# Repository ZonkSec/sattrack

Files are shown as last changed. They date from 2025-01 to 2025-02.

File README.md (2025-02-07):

# SatTrack
DIY Satellite Tracker for Ham Radio
* For [Arrow II Sat Antenna](https://www.arrowantennas.com/arrowii/146-437.html)
* improved 3D printed parts | [original design by jbyrns](https://www.thingiverse.com/thing:4664558)
* Nema 17 Motors
* on-board tracking software and battery
  * doubles as a counter weight; fewer wires to get tangled 
  * rasperby pi zero
  * custom pcb for:
    * A4988 Stepper Drivers
    * Power regulation
    * Buzzer output
    * Easy connectivity for switches and connections
  * full featured web interface
  * satellite definitions compatible with opengd77
 
 ## Repo Structure
 The repo is broken into several categories:
 * [3d models](3d%20models) - this contains all the 3d parts, as well as hardware needed
 * [app](app) - this contains the python application
 * [hardware](hardware) - this contains the custom pcb

Each category contains it's own readme.md with more details.

 ## Images
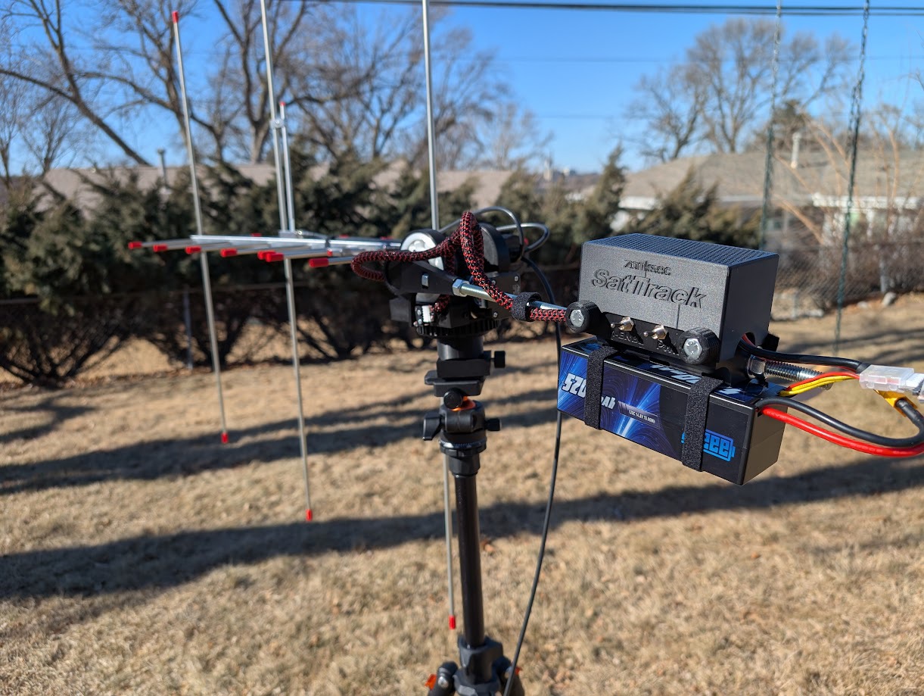
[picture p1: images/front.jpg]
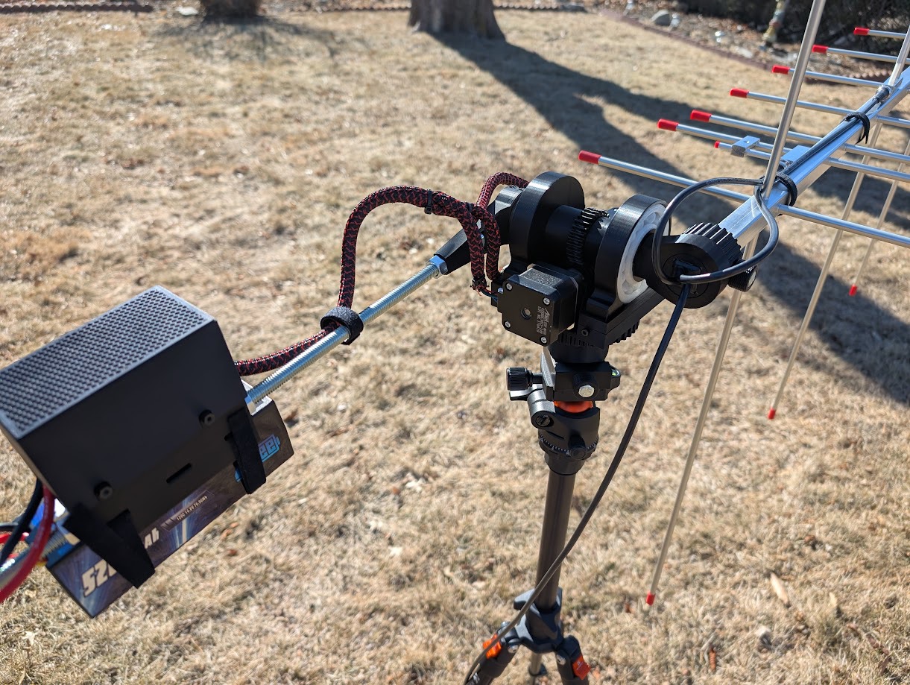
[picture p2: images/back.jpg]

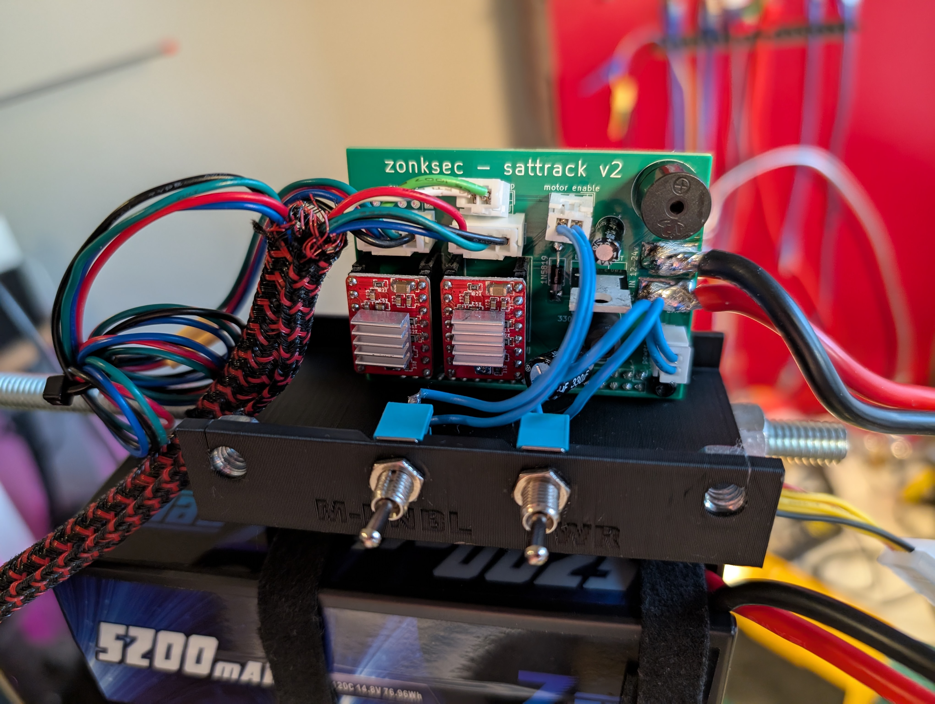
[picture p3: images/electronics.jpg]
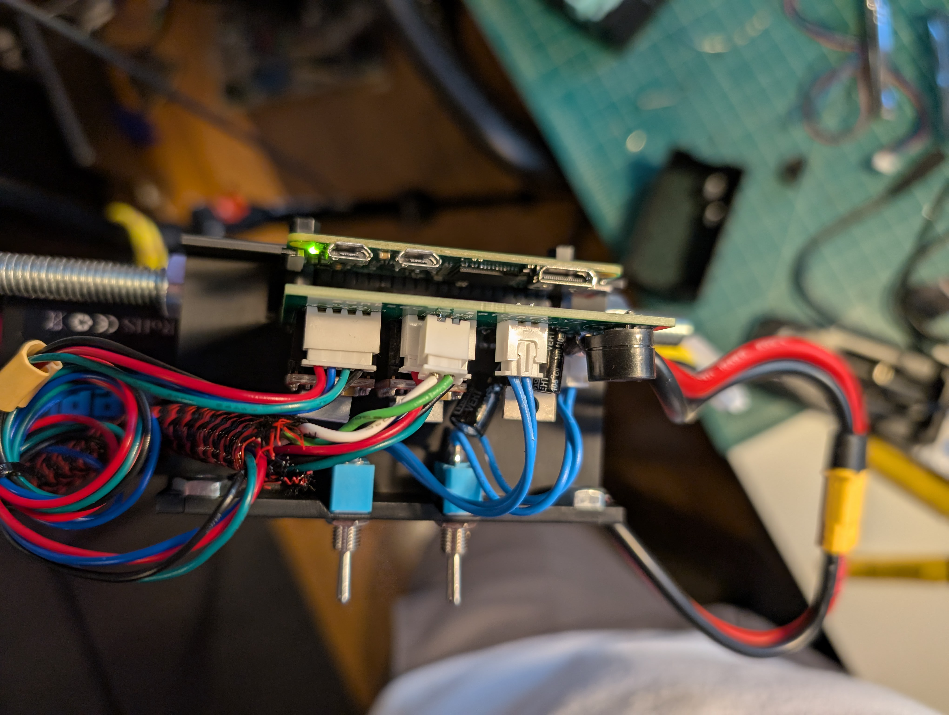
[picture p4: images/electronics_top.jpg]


<div align="center">
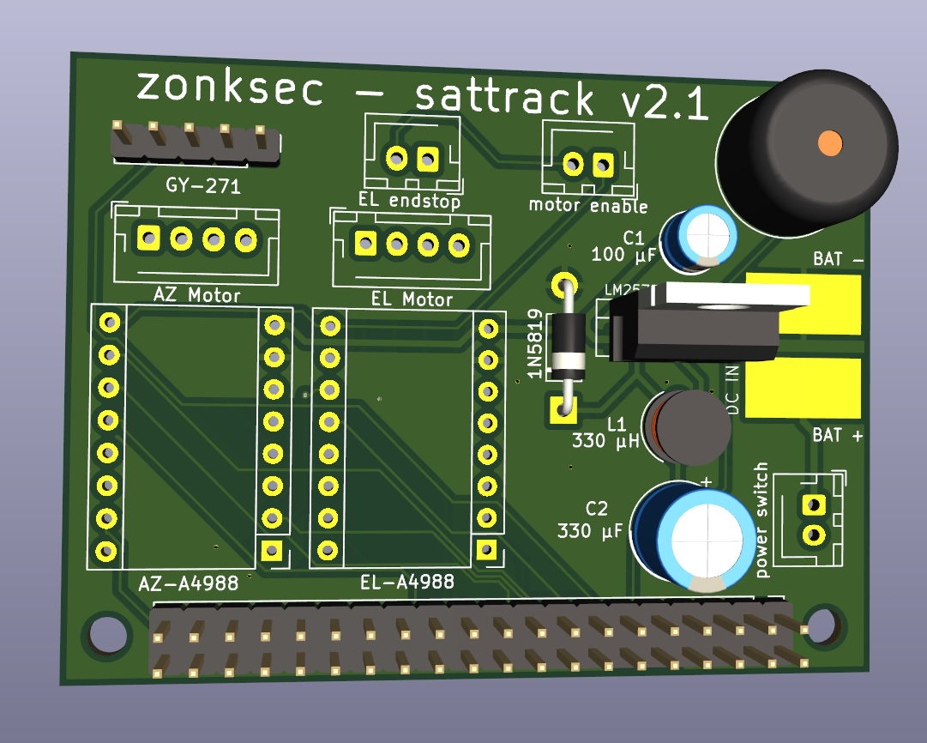
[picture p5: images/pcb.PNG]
 
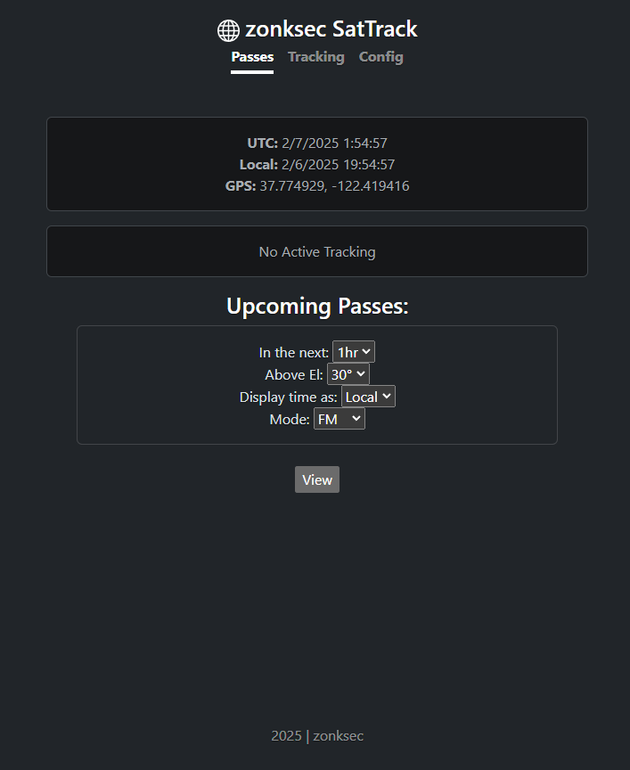
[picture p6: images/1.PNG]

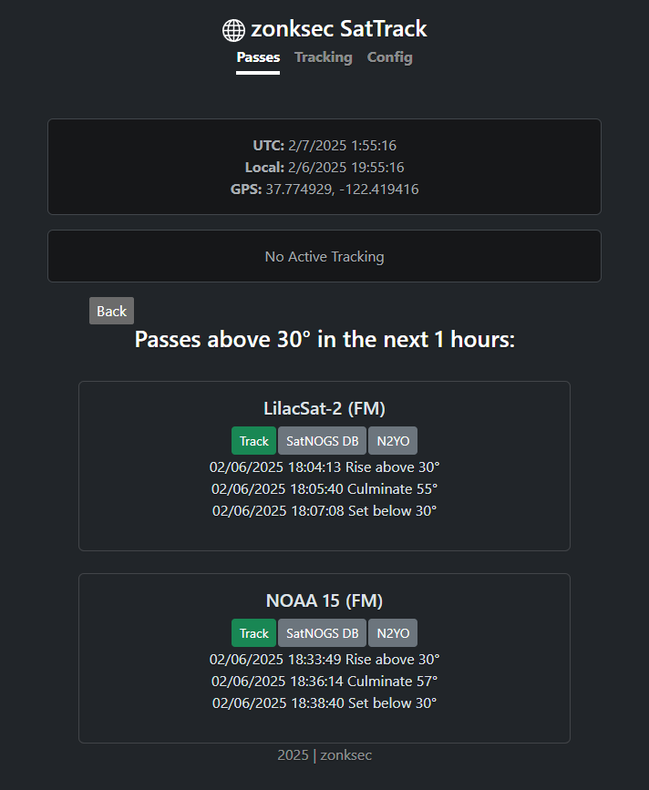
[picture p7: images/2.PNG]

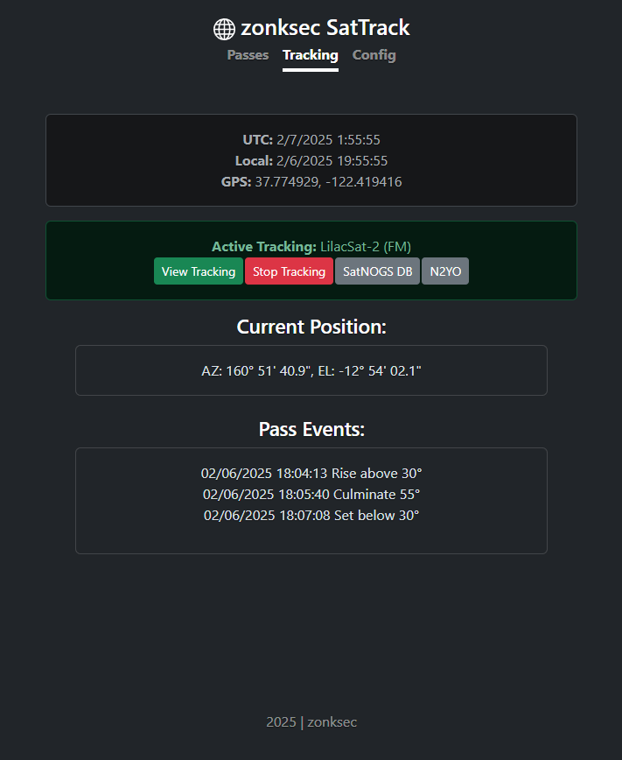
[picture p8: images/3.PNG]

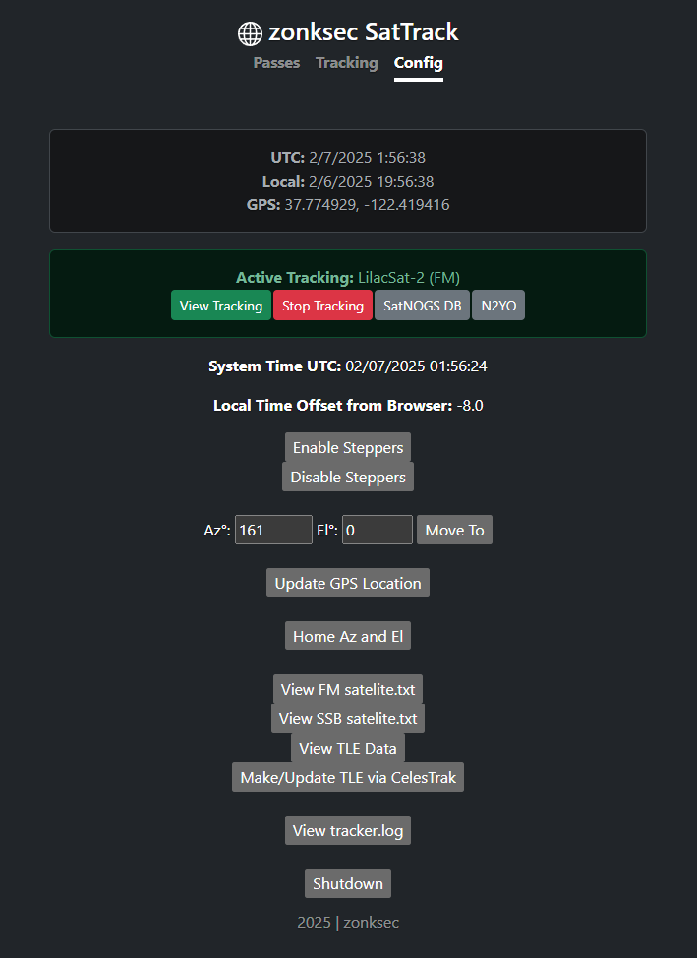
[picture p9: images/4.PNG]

</div>

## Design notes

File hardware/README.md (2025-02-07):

# Hardware

## Parts Needed:
* 1x Custom PCB
* 1x Raspberry Pi Zero W 1 or 2 (other RPis may work, but these are the only I've tested)
* 2x A4988 Stepper Drivers
* 2x "3d pritner" motor wires (depends on your motor, but mine was the standard 4pin XH 2.54 <-> 6pin PH 2.0)
* 2x Nema 17 Stepper Motors
* 1x 100 µF capacitor (C1)
* 1x 330 µF capacitor (C2)
* 1x 1N5819 Diode (D1)
* 1x 330 µH inductor (L1)
* 1x LM2575 5v switching reg (U1)
* 1x Passive Buzzer (BZ1)
* 2x Mini Toggle Switches ([Link](https://www.amazon.com/dp/B0799LBFNY?))
* 3x JST-XH 2.5pitch 2pin parts for motor enable switch, on/off switch, EL endspot microswitch
* 2x JST-XH 2.5pitch 4pin parts for motor connectors
* 1x Micro Limit Switch KW12-3 for EL limit switch
* 1x Battery connector and wires (I used XT60)
* 1x LiPo Battery ([Link to what I use](https://www.amazon.com/gp/product/B0D59XCQ3Z))
* 1x Roll of 1/2in Hook & Loop Straps to strap battery on
* 1x RC Battery Alarm to monitor voltage

<div align="center">

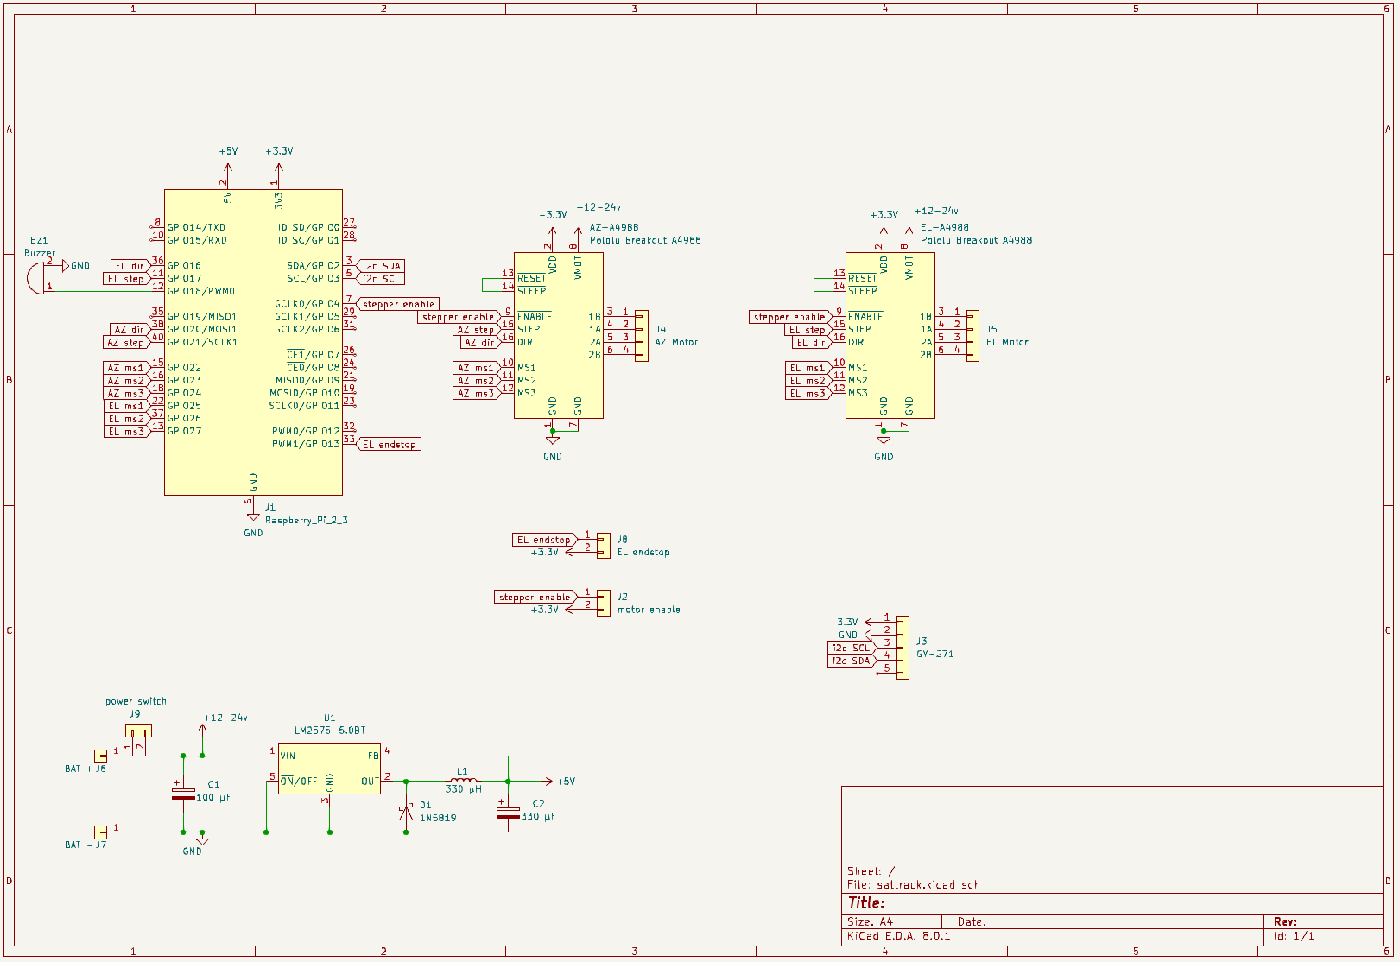
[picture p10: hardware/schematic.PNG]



</div>

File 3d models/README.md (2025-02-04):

# 3D Models
Original credit goes to jbyrns - https://www.thingiverse.com/thing:4664558

## Revised
* revised_Base.stl - made main bolt have a hex top, so can be tighted from below after assembly and wont spit
* revised_Counter.stl - changed this counter weight arm to have neccessary spacing to make room for microswitch EL endstop
* revised_GearSmall.stl - changed this gear to fit standard m3 nut snuggly 
* revised_Thrust.stl - made room so this part can accomadate the bolt and nut, while still fitting in tripod
* revised_WormConnector.stl - changed this gear to fit standard m3 nut snuggly 
  
## New
* new_EBbox_base.stl - electronic battery box bottom. this serves as the counter weight 
* new_EBbox_top.stl - electronic battery box top. this serves as the counter weight 
* new_endstop_arm.stl - this arm is engaged with main shaft (TrackArm) and can be used to home/zero the EL axis using a microswitch
* new_endstop_switch_bracket.stl - this bracket holds the microswitch for EL homing. bolts onto Base.stl
* new_quaterinch_knob.stl - knob for 1/4 bolt. used in adapter plate, trackarmknob, and EBbox
* new_universal_adapter_plate.stl - adapter plate for tripods whose quick release doesnt fit Thrust.stl. can attach to any 1/4 threaded plate
* new_wrench.stl - wrench to tighten parts on the 3/8th threaded rod.
  
## Original
* original_BearingHousing.STL
* original_Clip.STL
* original_Gear.STL
* original_TrackArm.STL
* original_TrackArmKnob.STL
* original_Worm.STL
* original_WormBase.STL
* original_bearing_all_fixed.stl
* original_collar.STL

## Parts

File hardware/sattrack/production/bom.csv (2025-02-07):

Designator | Footprint | Quantity | Value | LCSC Part #
AZ-A4988, EL-A4988 | Pololu_Breakout-16_15.2x20.3mm | 2 | Pololu_Breakout_A4988
BZ1 | Buzzer_12x9.5RM7.6 | 1 | Buzzer
C1 | CP_Radial_D5.0mm_P2.50mm | 1 | 100 µF
C2 | CP_Radial_D8.0mm_P3.80mm | 1 | 330 µF
D1 | D_DO-41_SOD81_P10.16mm_Horizontal | 1 | 1N5819
J1 | PinHeader_2x20_P2.54mm_Vertical | 1 | Raspberry_Pi_2_3
J2 | JST_XH_B2B-XH-AM_1x02_P2.50mm_Vertical | 1 | motor enable
J3 | PinHeader_1x05_P2.54mm_Vertical | 1 | GY-271
J4 | JST_XH_B4B-XH-AM_1x04_P2.50mm_Vertical | 1 | AZ Motor
J5 | JST_XH_B4B-XH-AM_1x04_P2.50mm_Vertical | 1 | EL Motor
J6 | SolderWirePad_1x01_SMD_5x10mm | 1 | BAT +
J7 | SolderWirePad_1x01_SMD_5x10mm | 1 | BAT -
J8 | JST_XH_B2B-XH-AM_1x02_P2.50mm_Vertical | 1 | EL endstop
J9 | JST_XH_B2B-XH-AM_1x02_P2.50mm_Vertical | 1 | power switch
L1 | L_Radial_D6.0mm_P4.00mm | 1 | 330 µH
U1 | TO-220-5_Vertical | 1 | LM2575-5.0BT

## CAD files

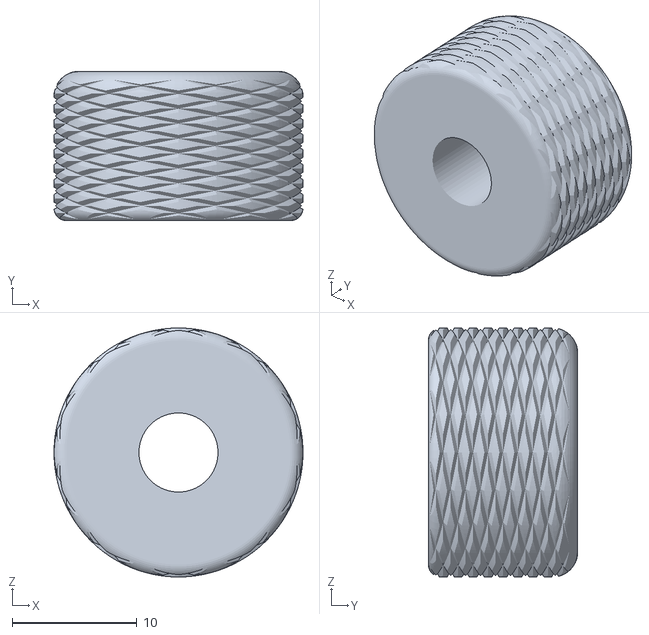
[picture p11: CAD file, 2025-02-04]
3d models/new_quaterinch_knob.stl
20.0 x 12.0 x 20.0

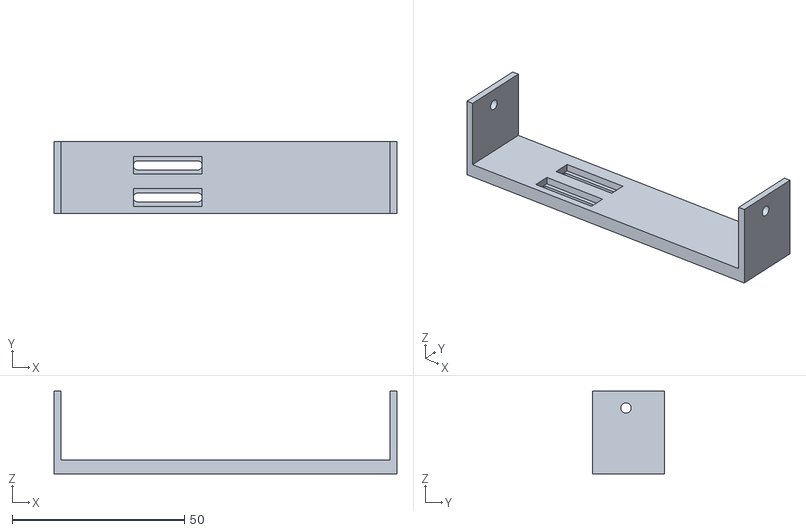
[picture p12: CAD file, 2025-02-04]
3d models/new_endstop_switch_bracket.stl
99.5 x 21.0 x 24.0

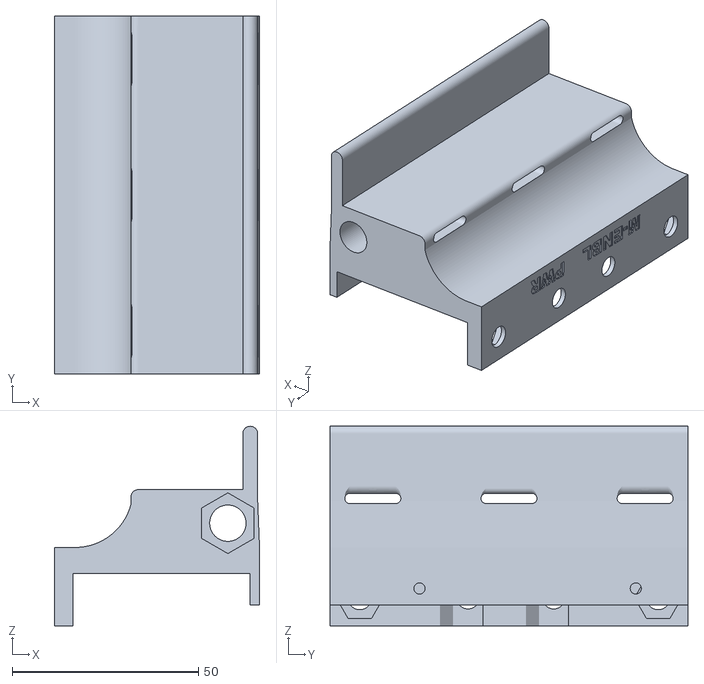
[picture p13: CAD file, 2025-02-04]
3d models/new_EBbox_base.stl
55.0 x 96.0 x 53.5

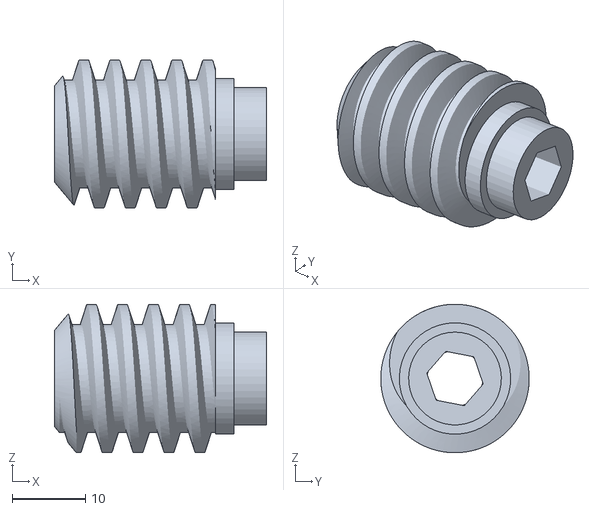
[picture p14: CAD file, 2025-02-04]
3d models/original_Worm.STL
29.0 x 20.3 x 20.3

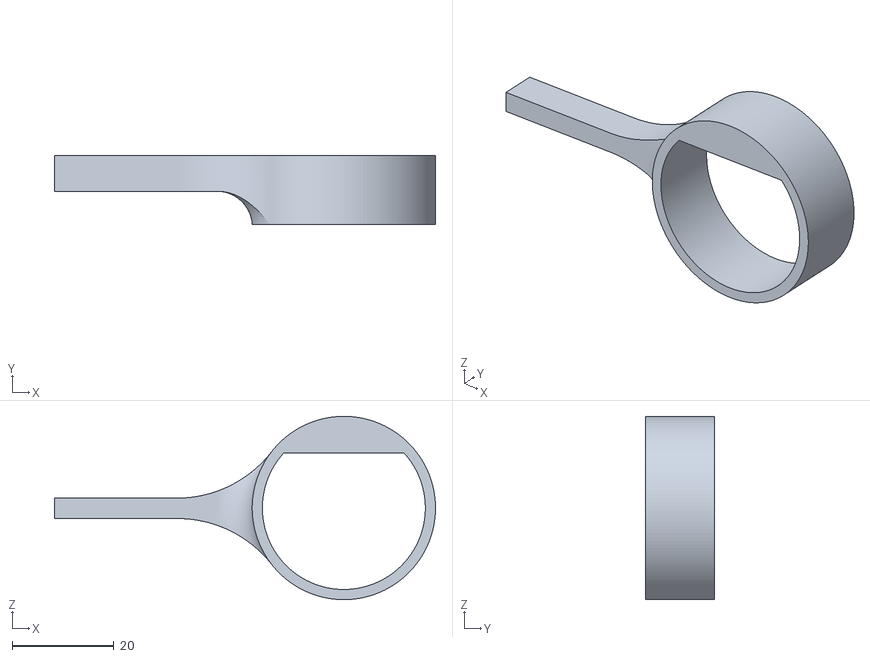
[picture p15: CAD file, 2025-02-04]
3d models/new_endstop_arm.stl
74.8 x 13.5 x 36.0

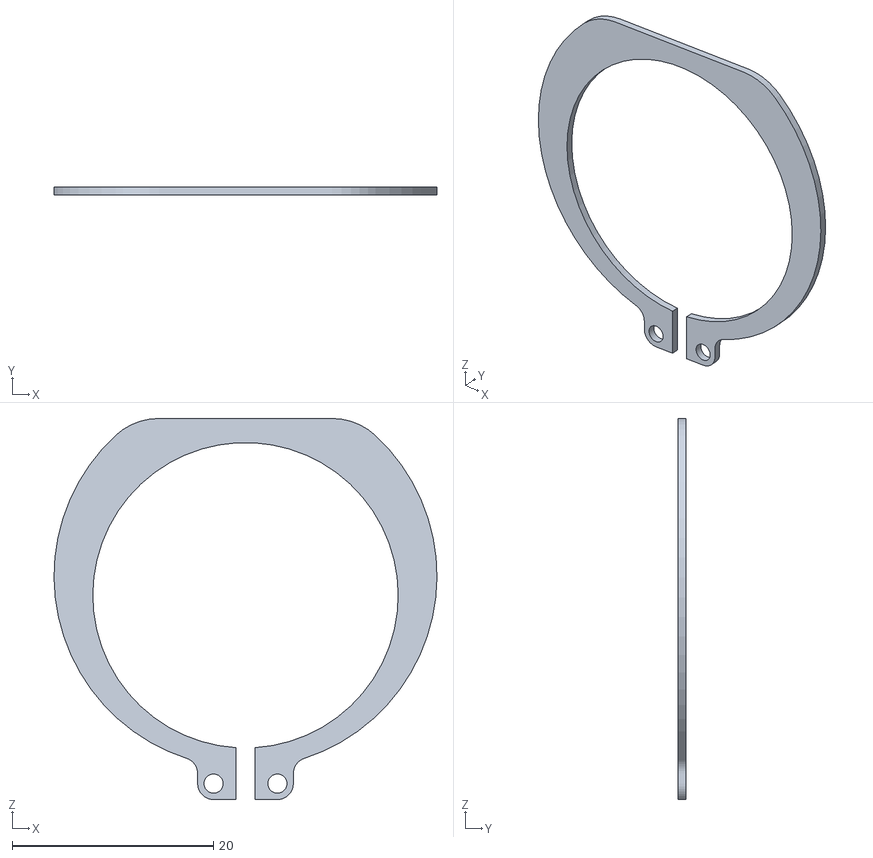
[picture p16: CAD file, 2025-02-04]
3d models/original_Clip.STL
38.1 x 0.826 x 37.9

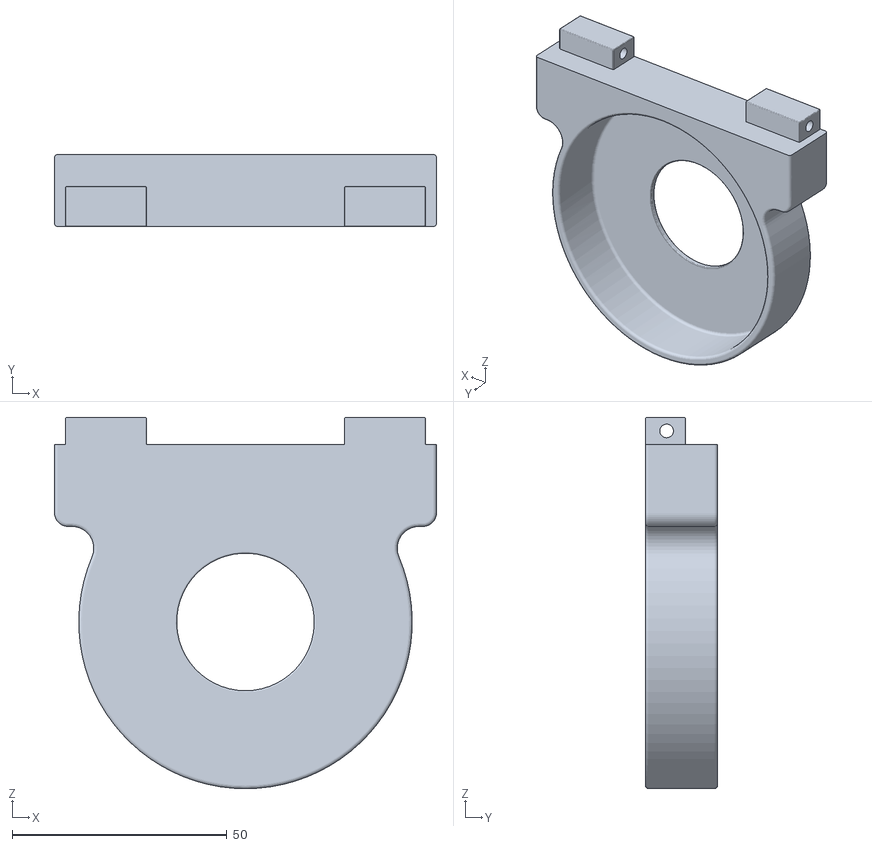
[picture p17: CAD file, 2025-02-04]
3d models/original_BearingHousing.STL
88.9 x 16.8 x 86.4

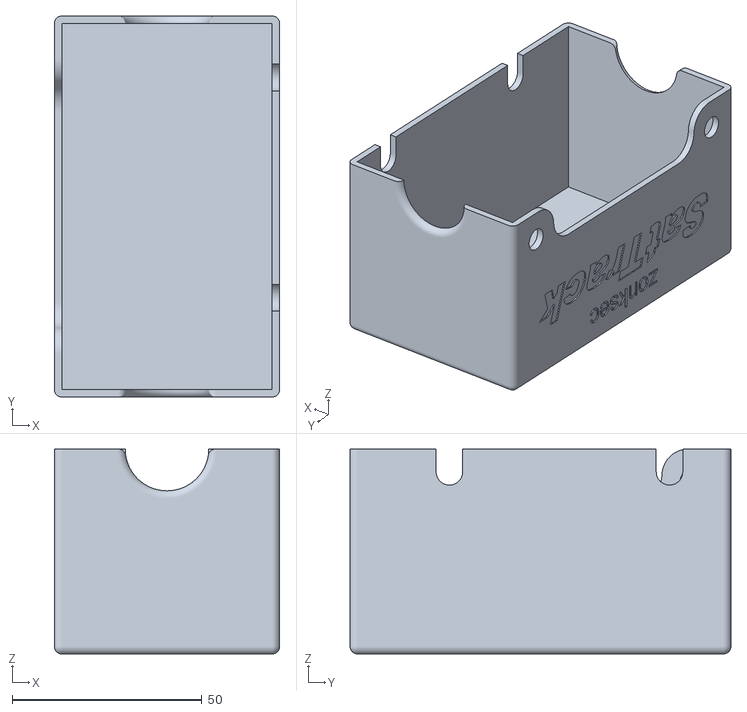
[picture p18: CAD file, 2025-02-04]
3d models/new_EBbox_top.stl
59.4 x 100.4 x 54.0

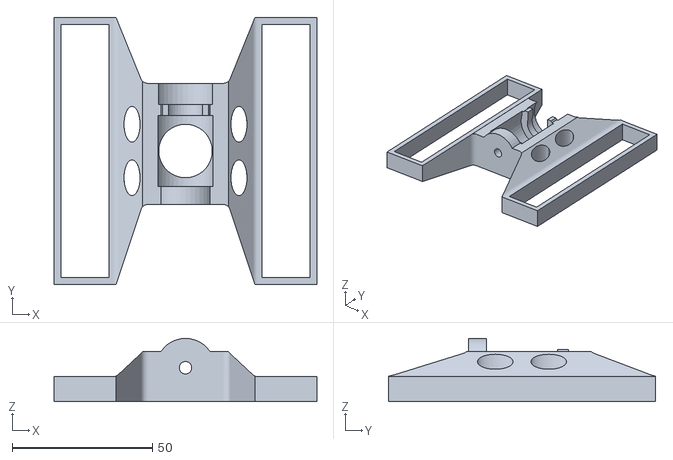
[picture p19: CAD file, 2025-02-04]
3d models/original_WormBase.STL
93.7 x 95.3 x 22.5

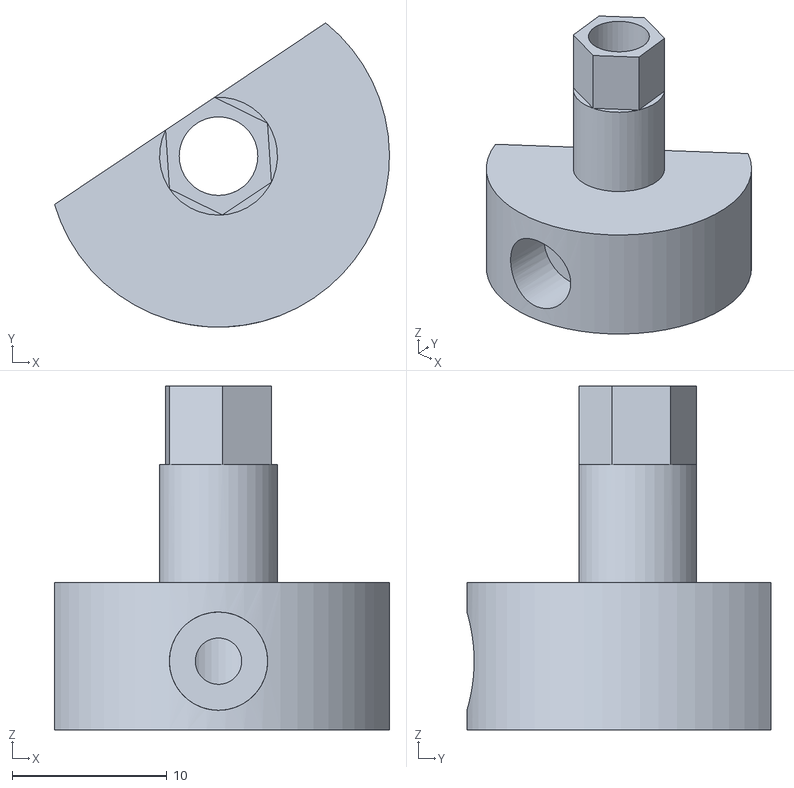
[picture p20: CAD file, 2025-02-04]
3d models/revised_WormConnector.stl
21.6 x 19.7 x 22.2

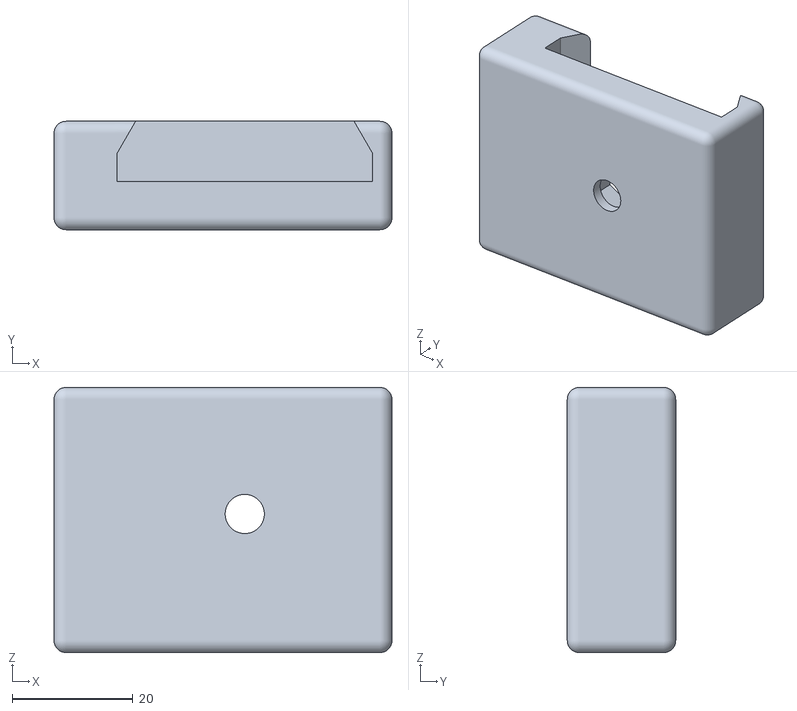
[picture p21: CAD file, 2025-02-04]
3d models/new_universal_adapter_plate.stl
56.1 x 18.0 x 44.0

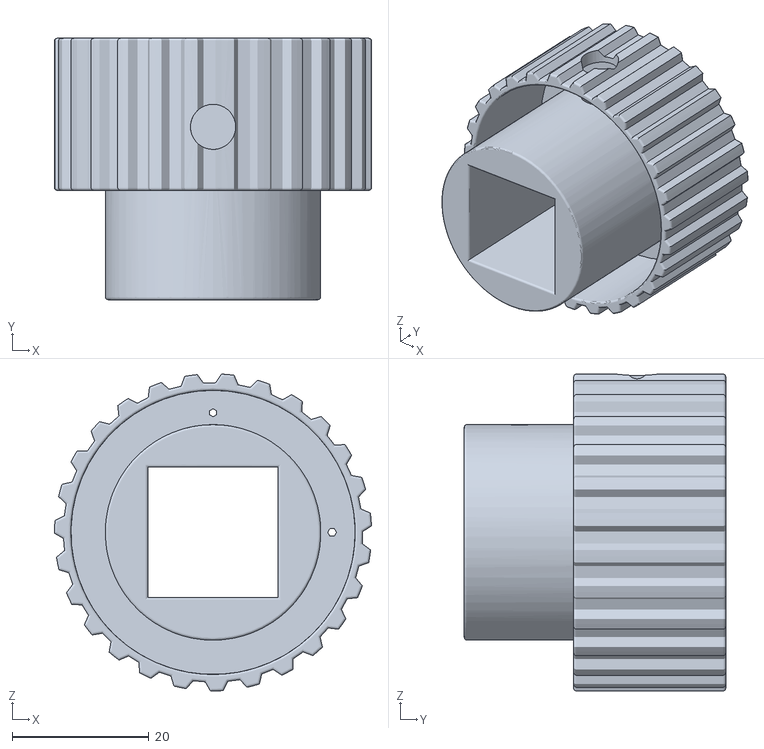
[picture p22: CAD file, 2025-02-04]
3d models/original_TrackArmKnob.STL
46.3 x 38.2 x 46.3

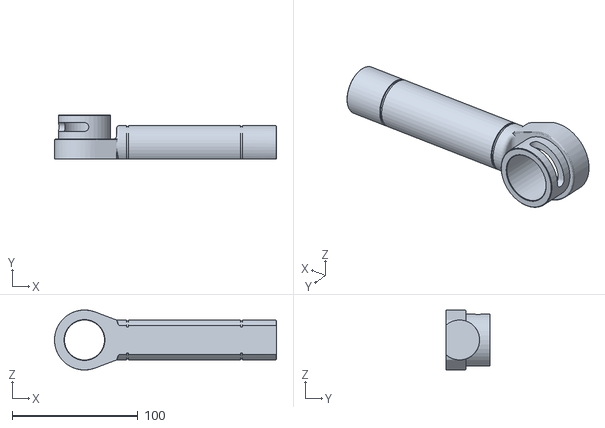
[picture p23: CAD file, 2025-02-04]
3d models/original_TrackArm.STL
176.2 x 34.9 x 47.6

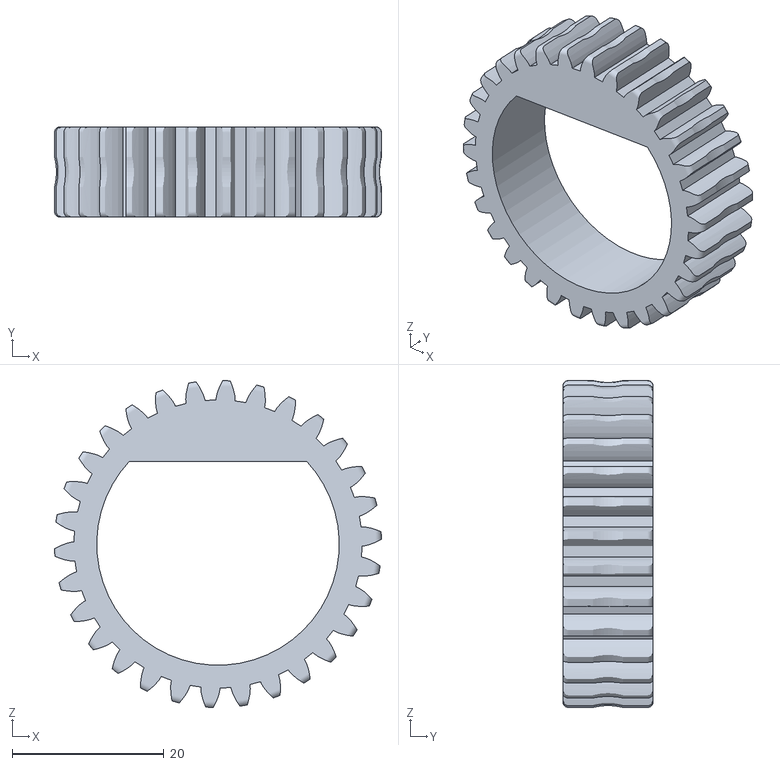
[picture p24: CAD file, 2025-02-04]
3d models/original_Gear.STL
43.2 x 11.9 x 43.2

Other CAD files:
3d models/new_wrench.stl
3d models/revised_Base.stl
3d models/revised_Thrust.stl
3d models/revised_GearSmall.stl
3d models/original_bearing_all_fixed.stl
3d models/original_collar.STL
3d models/revised_Counter.stl

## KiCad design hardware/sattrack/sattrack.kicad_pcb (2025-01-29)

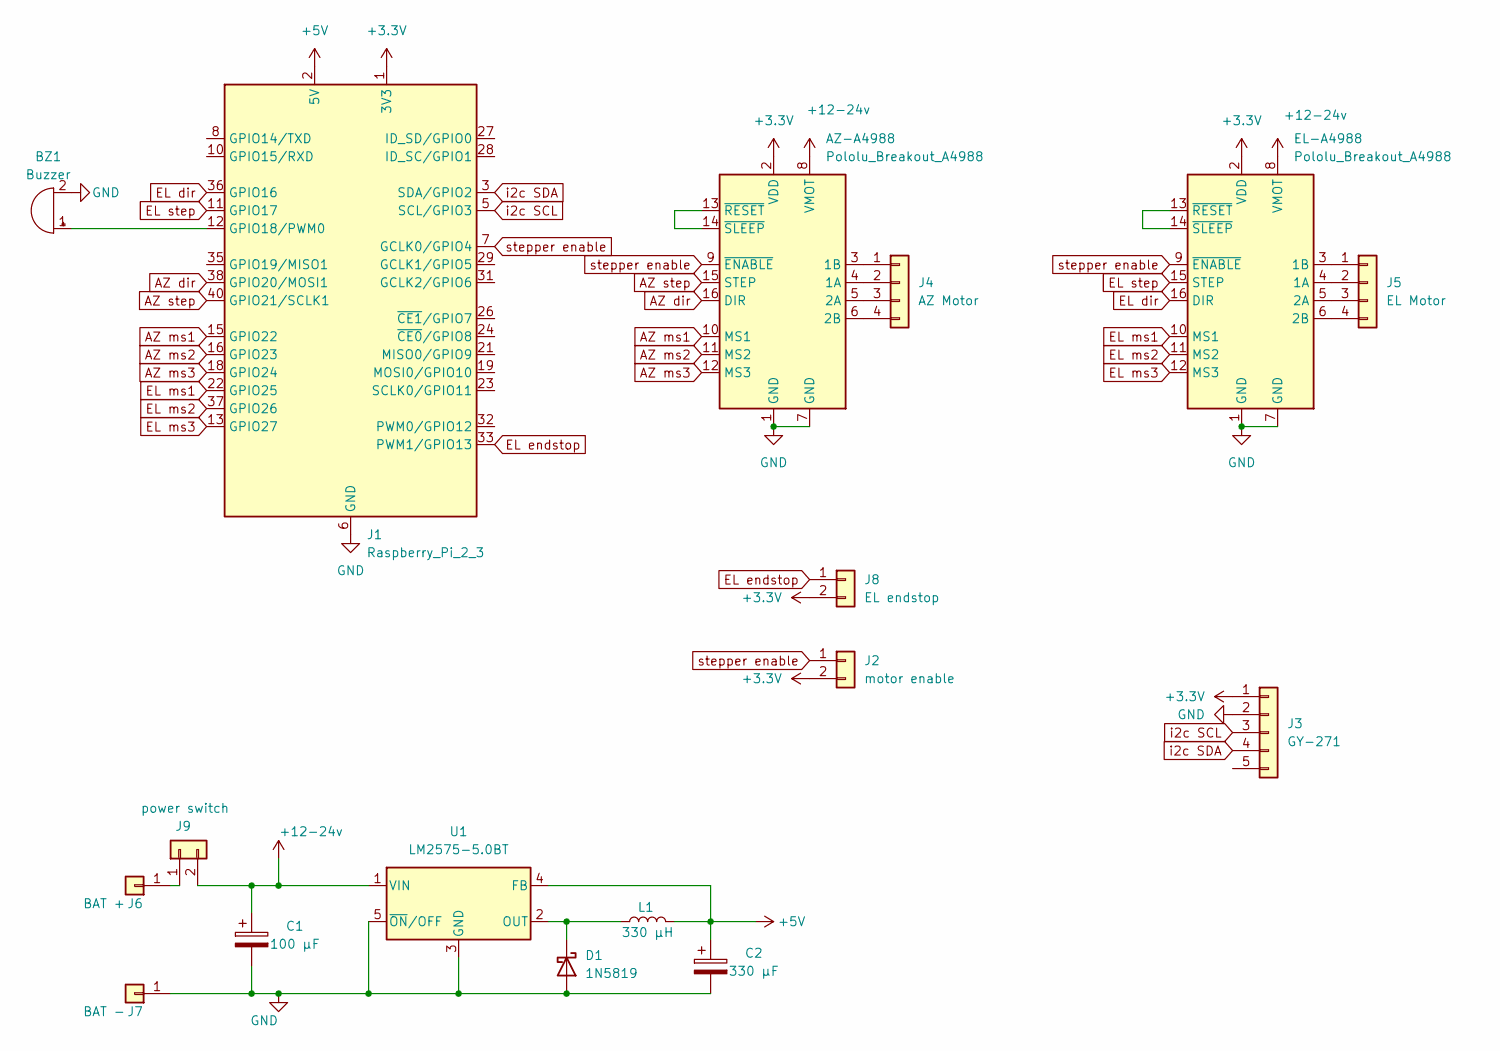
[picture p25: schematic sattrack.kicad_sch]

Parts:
AZ-A4988: Pololu_Breakout_A4988; Pololu_Breakout-16_15.2x20.3mm
BZ1: Buzzer; Buzzer_12x9.5RM7.6
C1: 100 µF; CP_Radial_D5.0mm_P2.50mm
C2: 330 µF; CP_Radial_D8.0mm_P3.80mm
D1: 1N5819; D_DO-41_SOD81_P10.16mm_Horizontal
EL-A4988: Pololu_Breakout_A4988; Pololu_Breakout-16_15.2x20.3mm
J1: Raspberry_Pi_2_3; PinHeader_2x20_P2.54mm_Vertical
J2: motor enable; JST_XH_B2B-XH-AM_1x02_P2.50mm_Vertical
J3: GY-271; PinHeader_1x05_P2.54mm_Vertical
J4: AZ Motor; JST_XH_B4B-XH-AM_1x04_P2.50mm_Vertical
J5: EL Motor; JST_XH_B4B-XH-AM_1x04_P2.50mm_Vertical
J6: BAT +; SolderWirePad_1x01_SMD_5x10mm
J7: BAT -; SolderWirePad_1x01_SMD_5x10mm
J8: EL endstop; JST_XH_B2B-XH-AM_1x02_P2.50mm_Vertical
J9: power switch; JST_XH_B2B-XH-AM_1x02_P2.50mm_Vertical
L1: 330 µH; L_Radial_D6.0mm_P4.00mm
U1: LM2575-5.0BT; TO-220-5_Vertical

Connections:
+3.3V: AZ-A4988.2 (VDD), EL-A4988.2 (VDD), J1.1 (3V3), J1.17 (3V3), J2.2, J3.1, J8.2
+5V: C2.1, J1.2 (5V), J1.4 (5V), L1.2, U1.4 (FB)
+12-24v: AZ-A4988.8 (VMOT), C1.1, EL-A4988.8 (VMOT), J9.2, U1.1 (VIN)
AZ dir: AZ-A4988.16 (DIR), J1.38 (GPIO20/MOSI1)
AZ ms1: AZ-A4988.10 (MS1), J1.15 (GPIO22)
AZ ms2: AZ-A4988.11 (MS2), J1.16 (GPIO23)
AZ ms3: AZ-A4988.12 (MS3), J1.18 (GPIO24)
AZ step: AZ-A4988.15 (STEP), J1.40 (GPIO21/SCLK1)
EL dir: EL-A4988.16 (DIR), J1.36 (GPIO16)
EL endstop: J1.33 (PWM1/GPIO13), J8.1
EL ms1: EL-A4988.10 (MS1), J1.22 (GPIO25)
EL ms2: EL-A4988.11 (MS2), J1.37 (GPIO26)
EL ms3: EL-A4988.12 (MS3), J1.13 (GPIO27)
EL step: EL-A4988.15 (STEP), J1.11 (GPIO17)
GND: AZ-A4988.1 (GND), AZ-A4988.7 (GND), BZ1.2 (-), C1.2, C2.2, D1.2 (A), EL-A4988.1 (GND), EL-A4988.7 (GND), J1.6 (GND), J1.9 (GND), J1.14 (GND), J1.20 (GND), J1.25 (GND), J1.30 (GND), J1.34 (GND), J1.39 (GND), J3.2, J7.1, U1.3 (GND), U1.5 (~ON/OFF)
unnamed: AZ-A4988.4 (1A), J4.2
unnamed: AZ-A4988.3 (1B), J4.1
unnamed: AZ-A4988.5 (2A), J4.3
unnamed: AZ-A4988.6 (2B), J4.4
unnamed: AZ-A4988.13 (~RESET), AZ-A4988.14 (~SLEEP)
unnamed: BZ1.1 (+), J1.12 (GPIO18/PWM0)
unnamed: D1.1 (K), L1.1, U1.2 (OUT)
unnamed: EL-A4988.4 (1A), J5.2
unnamed: EL-A4988.3 (1B), J5.1
unnamed: EL-A4988.5 (2A), J5.3
unnamed: EL-A4988.6 (2B), J5.4
unnamed: EL-A4988.13 (~RESET), EL-A4988.14 (~SLEEP)
unnamed: J6.1, J9.1
i2c SCL: J1.5 (SCL/GPIO3), J3.3
i2c SDA: J1.3 (SDA/GPIO2), J3.4
stepper enable: AZ-A4988.9 (~ENABLE), EL-A4988.9 (~ENABLE), J1.7 (GCLK0/GPIO4), J2.1

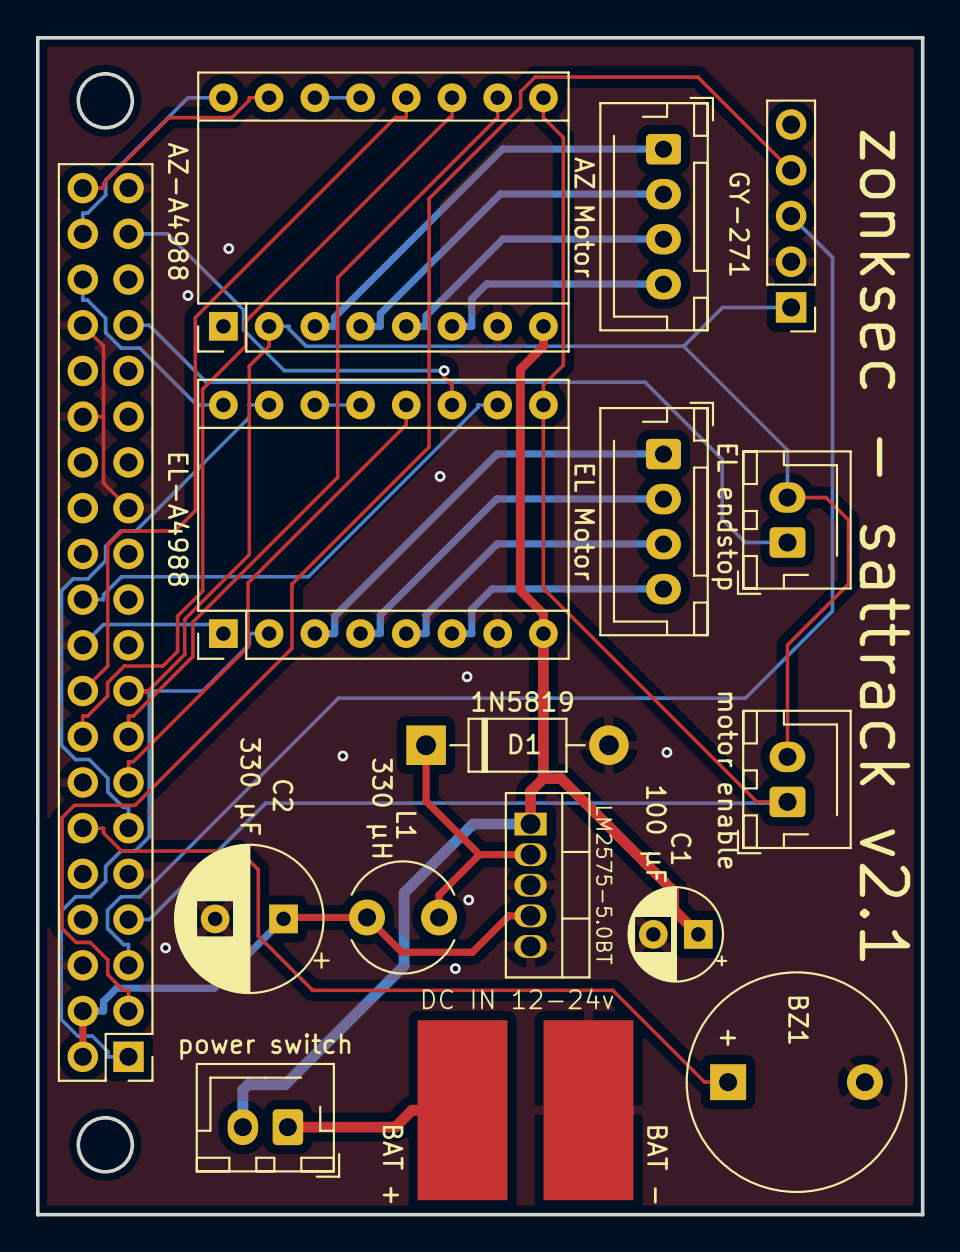
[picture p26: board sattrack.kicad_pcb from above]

Board: 2 copper layers, 49.2 x 65.4 mm, 17 parts (0 on the bottom side), 31 nets.

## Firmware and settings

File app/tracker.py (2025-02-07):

import os
import threading
from io import StringIO,BytesIO
from RpiMotorLib import RpiMotorLib
from flask import Flask,request, render_template, redirect,Response
import concurrent.futures
import signal
import RPi.GPIO as GPIO
import sys
from skyfield.api import load,wgs84
from skyfield.iokit import parse_tle_file
from datetime import timedelta,timezone,datetime
from time import sleep
import requests
import csv

if not os.path.exists("key.pem") or not os.path.exists("cert.pem"):
   print("no certs found. make sure openssl is installed. generating...")
   os.system("openssl req -x509 -newkey rsa:2048 -nodes -out cert.pem -keyout key.pem -days 3650 -subj '/C=/ST=/L=/O=/CN='")

global lat
global long
global location_tz_offset
lat = None
long = None
location_tz_offset = 0

global tracking_thread
global stop_tracking
global tracking_sat_name
global tracking_sat_pos
global tracking_sat_events
global tracking_sat_cat
tracking_thread = None
stop_tracking = False
tracking_sat_pos = ""
tracking_sat_name = ""
tracking_sat_events = ""
tracking_sat_cat = ""

app = Flask(__name__)

@app.route("/config") 
def config(): 
  global lat
  global long
  global tracking_sat_name
  global current_az_pos
  global current_el_pos
  global location_tz_offset
  global tracking_sat_cat

  now = datetime.utcnow().strftime('%m/%d/%Y %H:%M:%S')

  if GPIO.input(4) == 1:
    steppers_disabled = True
  else:
    steppers_disabled = False
  
  if lat == None or long == None:
    gpsmissing = True
  else:
    gpsmissing = False
  return render_template("config.html",tracking_sat_cat=tracking_sat_cat,location_tz_offset=location_tz_offset,now=now,current_az_pos=current_az_pos,current_el_pos=current_el_pos,steppers_disabled=steppers_disabled,tracking_sat_name=tracking_sat_name,gpsmissing=gpsmissing,lat=lat,long=long)

@app.route("/set_tz") 
def set_tz_offset(): 
   global location_tz_offset
   location_tz_offset = int(request.args.get('offset'))
   return redirect(request.referrer)

@app.route("/view") 
def view():
  file = request.args.get('file')
  if file == "fmsattxt":
    try:
      with open('data/fm/satellites.txt', 'r') as file:
        file_content = file.read()
    except:
       file_content = "satellites.txt not found"
  elif file == "trackerlog":
     try:
        with open('tracker.log', 'r') as file:
           file_content = file.read()
     except:
        file_content = "tracker.log not found"
  elif file == "ssbsattxt":
    try:
      with open('data/ssb/satellites.txt', 'r') as file:
        file_content = file.read()
    except:
       file_content = "satellites.txt not found"
  else:
     if os.path.exists("data/ssb/filtered_TLE.txt") and os.path.exists("data/fm/filtered_TLE.txt"):
        fm_satellites = open('data/fm/filtered_TLE.txt', 'r').read()
        ssb_satellites = open('data/ssb/filtered_TLE.txt', 'r').read()
        file_content = fm_satellites + ssb_satellites
     else:
        file_content = "tle data missing"
  return Response(file_content, mimetype='text/plain')



@app.route('/motorEnable')
def enable():
   x = request.args.get('enabled')
   if x == "yes":
      GPIO.output(4, GPIO.LOW)
      return redirect(request.referrer)
   else:
      GPIO.output(4, GPIO.HIGH)
      return redirect(request.referrer)

@app.route('/shutdown')
def shutdown():
   os.system("sudo shutdown -h now")  
   return "Shutting down..."
   
@app.route('/homeAZEL')
def homeAZEL():
    if GPIO.input(4) == 1:
       return("steppers are disabled. not homing")
    if tracking_thread != None:
       return("actively tracking a sat. not homing")
    zero_EL()
    global current_az_pos
    current_az_pos = 0
    return redirect(request.referrer)

global moving 
moving = False
@app.route('/moveTo')
def moveTo():
    global current_az_pos
    global current_el_pos
    global tracking_thread
    global moving 

    if tracking_thread == None and moving == False:
      moving = True
      desired_az_pos = int(request.args.get('az',default=current_az_pos))
      desired_el_pos = int(request.args.get('el',default=current_el_pos))
      az_steps, az_direction = az_deg_to_steps_dir(desired_az_pos)
      el_steps,el_direction = el_deg_to_steps_dir(desired_el_pos)
      thread_move_steps(az_direction,az_steps,el_direction,el_steps)
      if az_steps > 0:
        current_az_pos = desired_az_pos
      if el_steps > 0:
          current_el_pos = desired_el_pos
      moving = False
      return redirect(request.referrer)
    else:
       return "cant manual move. active tracking is ongoing. or a manual move is active"

@app.route('/updateTLE')
def updateTLE():
    msg =update_sat_data()
    return msg

@app.route("/") 
@app.route('/passes',methods=['GET', 'POST'])
def listUpcomingPasses():
  global lat
  global long
  global tracking_sat_name
  global location_tz_offset
  global tracking_sat_cat

  if GPIO.input(4) == 1:
    steppers_disabled = True
  else:
     steppers_disabled = False

  if lat == None or long == None:
      gpsmissing = True
  else:
     gpsmissing = False

  if request.method == 'GET':
    return render_template("passes.html",method=request.method,tracking_sat_cat=tracking_sat_cat,steppers_disabled=steppers_disabled,tracking_sat_name=tracking_sat_name,gpsmissing=gpsmissing,lat=lat,long=long)
  if request.method == 'POST':
    if gpsmissing:
      return "lat or long not set"
  
    time = request.form.get('time')
    display_time = request.form.get('display_time')
    max_el = int(request.form.get('el',default=30))
    mode = request.form.get('mode')

    if time == None or max_el == None:
       return "pass input not set"

    ts = load.timescale()
    if mode == "fm":
      if os.path.exists("data/fm/filtered_TLE.txt"):
        satellites= load.tle_file('data/fm/filtered_TLE.txt')
      else:
        return "filtered_TLE not found. create it using 'Make/Update TLE via CelesTrak' on Config page"
    elif mode == "ssb":
      if os.path.exists("data/ssb/filtered_TLE.txt"):
        satellites= load.tle_file('data/ssb/filtered_TLE.txt')
      else:
        return "filtered_TLE not found. create it using 'Make/Update TLE via CelesTrak' on Config page"
    elif mode == "both":
       if os.path.exists("data/ssb/filtered_TLE.txt") and os.path.exists("data/fm/filtered_TLE.txt"):
        fm_satellites = open('data/fm/filtered_TLE.txt', 'r').read()
        ssb_satellites = open('data/ssb/filtered_TLE.txt', 'r').read()
        both = fm_satellites + ssb_satellites
        f = BytesIO(str.encode(both))
        satellites = list(parse_tle_file(f, ts))
       else:
        return "filtered_TLE not found. create it using 'Make/Update TLE via CelesTrak' on Config page"
    else:
      return "error on mode selection"

    location = wgs84.latlon(lat, long)
    if display_time == "local":
      location_tz = timezone(timedelta(hours=location_tz_offset))
    else:
       location_tz = timezone(timedelta(hours=0))

    t0 = ts.now()
    t1 = ts.utc(t0.utc_datetime() + timedelta(hours=int(time)))

    passes = {}
    passes_satcat = {}

    for satellite in satellites:
        t, events = satellite.find_events(location, t0, t1, altitude_degrees=max_el)
        event_names = 'Rise above '+str(max_el)+'°', 'Culminate', 'Set below '+str(max_el)+'°'
        my_events = []
        if len(events) != 0:
            for ti, event in zip(t, events):
                if event == 1:
                    difference = satellite - location
                    topocentric = difference.at(ti)
                    alt, az, distance = topocentric.altaz()
                    name = event_names[event] + ' ' + str(round(alt.degrees)) +'°'
                    timestamp = ti.astimezone(location_tz).strftime('%m/%d/%Y %H:%M:%S')
                else:
                    name = event_names[event]
                    timestamp = ti.astimezone(location_tz).strftime('%m/%d/%Y %H:%M:%S')
                my_events.append(f'{timestamp} {name}')
            passes[satellite.name]=my_events
            passes_satcat[satellite.name]=satellite.model.satnum
    passes_sorted = {}
    for x in (sorted(passes,key=passes.get)):
       passes_sorted[x]=passes[x]
       
  return render_template("passes.html",tracking_sat_cat=tracking_sat_cat,passes_satcat=passes_satcat,steppers_disabled=steppers_disabled,method=request.method,tracking_sat_name=tracking_sat_name,passes=passes_sorted,time=time,max_el=max_el,lat=lat,long=long,gpsmissing=gpsmissing)



@app.route('/getGPS')
def getGPS():
   global lat
   global long
   global location_tz_offset
   lat_param = request.args.get('lat')
   long_param = request.args.get('long')
   if not lat_param or not long_param:
    return """
  <script>navigator.geolocation.getCurrentPosition(function(location) {
    fetch("/getGPS?lat="+location.coords.latitude+"&long="+location.coords.longitude+"&next=" + document.referrer+"&utcoffset="+new Date().getTimezoneOffset(),{method: "GET"})
    .then(response => {
        if (response.redirected) {window.location.href = response.url}
        })});
  </script>
  """
   else:
        lat = float(lat_param)
        long = float(long_param)
        next = request.args.get('next')
        location_tz_offset = (int(request.args.get('utcoffset'))/60) * -1
        return redirect(next)

@app.route('/startTrack')
def track():
   global tracking_thread
   global tracking_sat_name
   global lat
   global long
   global tracking_sat_events
   sat = request.args.get('sat')
   if request.args.get('events'):
      tracking_sat_events = request.args.get('events').strip('[]').replace("\'", '').split(',')
   if lat == None or long == None:
     return "cant track. lat long not set"
   if tracking_thread is None:
      tracking_thread = threading.Thread(target = tracker, kwargs={'requested_sat':sat})
      tracking_thread.start()
      tracking_sat_name = sat
      return redirect("track")
   else:
        return("tracking already running. must kill first")

@app.route('/killTrack')
def stop():
    global stop_tracking
    global tracking_thread
    global tracking_sat_name
    global tracking_sat_events
    global tracking_sat_cat
    if tracking_thread is None:
        return redirect(request.referrer)
    else:
        stop_tracking = True
        tracking_thread.join()
        tracking_thread = None
        stop_tracking = False
        tracking_sat_name = ""
        tracking_sat_events = ""
        tracking_sat_cat = ""
        return redirect(request.referrer)

@app.route('/watchTracking')
def watch_track():
    global tracking_thread
    global tracking_sat_pos

    if tracking_thread is None:
        return "nothing is being track"
    else:
        def track_now():
            global tracking_sat_pos
            data = ""
            while True:
                data = tracking_sat_pos
                sleep(.1)
                yield data
    return track_now()

@app.route('/track')
def viewtrack():
    global tracking_thread
    global tracking_sat_pos
    global tracking_thread
    global tracking_sat_name
    global lat
    global long
    global tracking_sat_events
    global tracking_sat_cat

    if GPIO.input(4) == 1:
      steppers_disabled = True
    else:
      steppers_disabled = False

    if lat == None or long == None:
      gpsmissing = True
    else:
      gpsmissing = False

    sat_name_list = []
    if tracking_sat_name == "":
      with open('data/fm/satellites.txt', 'r') as csvfile:
        csvreader = csv.reader(csvfile)
        next(csvreader) #skip header line
        for row in csvreader:
          sat_name_list.append(row[1].strip())
      with open('data/ssb/satellites.txt', 'r') as csvfile:
        csvreader = csv.reader(csvfile)
        next(csvreader) #skip header line
        for row in csvreader:
          sat_name_list.append(row[1].strip())



    sat_name_list = sorted(sat_name_list)

    return render_template("tracking.html",tracking_sat_cat=tracking_sat_cat,tracking_sat_events=tracking_sat_events,steppers_disabled=steppers_disabled,tracking_sat_name=tracking_sat_name,sat_name_list=sat_name_list,tracking_thread=tracking_thread,lat=lat,long=long,gpsmissing=gpsmissing)

@app.after_request
def add_static_cache(response):
   if response.content_type in ["text/javascript; charset=utf-8",
                                "image/svg+xml; charset=utf-8",
                                "text/css; charset=utf-8",
                                "application/octet-stream"]:
      response.headers['Cache-Control'] = 'max-age=86400, public'  # Cache for 24 hours
   return response

GPIO.setwarnings(False)
GPIO.setmode(GPIO.BCM)
GPIO.setup(4, GPIO.OUT)#enable pin 
GPIO.output(4, GPIO.HIGH)#enable pin
GPIO.setup(13, GPIO.IN, pull_up_down=GPIO.PUD_DOWN) #endstop pin
GPIO.setup(18, GPIO.OUT) #buzzer pin

az_direction_pin = 20      
az_step_pin = 21
az_mode_pins = 22, 23, 24
az_a4988_nema = RpiMotorLib.A4988Nema(az_direction_pin, az_step_pin, az_mode_pins, "A4988")

el_direction_pin = 16    
el_step_pin = 17
el_mode_pins = 25, 26, 27
el_a4988_nema = RpiMotorLib.A4988Nema(el_direction_pin, el_step_pin, el_mode_pins, "A4988")

#full steps per rot = 200
#1/16 stepping steps per rot = 3200
#az gears 10:43 == 1:4.3
#az quater stepping full rotate steps = 13760
#az degs to steps = 13760/360 = 38.2222222222
steps_per_azDeg = 13760/360

#full steps per rot = 200
#1/4 stepping steps per rot = 800
#el gears 1:30
#el quater stepping full rotate steps = 24000
#el degs to steps = 24000 / 360 = 5.5555
steps_per_elDeg = 24000 / 360

global current_az_pos
global current_el_pos
current_az_pos = 0 
current_el_pos = 0


def buzz(freq,length):
  p = GPIO.PWM(18, freq)
  p.start(1)
  sleep(length)
  p.stop()

buzz(293*2,0.2)
buzz(329*2,0.2)
buzz(261*2,0.2)
buzz(130*2,0.2)
buzz(196*2,0.2)

def thread_move_steps(az_direction,az_steps,el_direction,el_steps):
  with concurrent.futures.ThreadPoolExecutor() as executor:
          az_steptype = "1/16"
          az_stepdelay = 0.0015
          az_initialdelay = 0.05
          el_steptype = "1/4"
          el_stepdelay = 0.0005
          el_initialdelay = 0.05
          f1 = executor.submit(az_a4988_nema.motor_go, az_direction, az_steptype , az_steps, az_stepdelay, False, az_initialdelay)
          f2 = executor.submit(el_a4988_nema.motor_go, el_direction, el_steptype , el_steps, el_stepdelay, False, el_initialdelay)
          

def az_deg_to_steps_dir(desired_az_pos):
  global current_az_pos
  print(f'current_az_pos: {current_az_pos}')
  if desired_az_pos > current_az_pos:
    deg_to_move = desired_az_pos - current_az_pos
    if deg_to_move > 180:
      #the other direction is shorter
      deg_to_move = 360 - (desired_az_pos - current_az_pos) 
      az_steps = int(deg_to_move * steps_per_azDeg)
      az_direction = True
    else: 
      az_steps = int(deg_to_move * steps_per_azDeg)
      az_direction = False
    
  if desired_az_pos < current_az_pos:
    deg_to_move = current_az_pos - desired_az_pos
    if deg_to_move > 180:
      #the other direction is shorter
      deg_to_move = 360 - (current_az_pos - desired_az_pos)
      az_steps = int(deg_to_move * steps_per_azDeg)
      az_direction = False
    else:
      az_steps = int(deg_to_move * steps_per_azDeg)
      az_direction = True
  
  if desired_az_pos == current_az_pos:
    #already at the AZ needed
    az_steps=0
    az_direction=True

  return az_steps, az_direction

def el_deg_to_steps_dir(desired_el_pos):
  global current_el_pos
  print(f'current_el_pos: {current_el_pos}')
  if desired_el_pos >= 0:
    if desired_el_pos > current_el_pos:
      deg_to_move = desired_el_pos - current_el_pos
      el_direction = True
      el_steps = int(deg_to_move * steps_per_elDeg)
    if desired_el_pos < current_el_pos:
      deg_to_move = current_el_pos - desired_el_pos
      el_steps = int(deg_to_move * steps_per_elDeg)
      el_direction = False
    if desired_el_pos == current_el_pos:
      #already at the EL needed
      el_steps=0
      el_direction=False
  else:
     el_steps = 0
     el_direction = True
    
  return el_steps,el_direction
  
def update_sat_data():
  url = 'https://celestrak.org/NORAD/elements/gp.php?GROUP=active&FORMAT=tle'
  r = requests.get(url, allow_redirects=True)
  open('data/celestrakTLEdata.txt', 'wb').write(r.content)
  missing_sats = []
  for mode in ["fm","ssb"]:
    satcat_list = []
    name_satcat_lookup = {}
    with open(f'data/{mode}/satellites.txt', 'r') as csvfile:
        csvreader = csv.reader(csvfile)
        next(csvreader) #skip header line
        for row in csvreader:
            name_satcat_lookup[row[0].strip()] = row[1].strip()
            satcat_list.append(row[0].strip())

    

    filtered_file = open(f'data/{mode}/filtered_TLE.txt', 'w')

    file = open('data/celestrakTLEdata.txt', 'r')
    lines = file.readlines()
    x = 0
    satcat_list = sorted(set(satcat_list)) # remove dups if any
    for x in range(len(lines)):
        if x%3==0:
            name = lines[x].strip()
            tle1 = lines[x+1].strip()
            tle2 = lines[x+2].strip()
            satcat = tle1[2:8]
            if satcat in satcat_list:
                filtered_file.write(name_satcat_lookup[satcat] + " ("+mode.upper()+")\n")
                filtered_file.write(tle1 + "\n")
                filtered_file.write(tle2 + "\n")
                satcat_list.remove(satcat)
                if len(satcat_list) == 0:
                  #got all the sats we need, stop processing
                  break
    if len(satcat_list) != 0:
       missing_sats.append(satcat_list)

  if len(missing_sats) != 0:
     #couldnt find tle for a sat
     return ("TLEs updated. couldnt find the following TLEs from satellites.txt in celestrak data: "+str(missing_sats))
  else:
     return "TLEs updated"

def handler(signum,frame):
  print("exiting... stopping motors and cleaning up GPIO")        
  az_a4988_nema.motor_stop()
  el_a4988_nema.motor_stop()
  GPIO.output(4, GPIO.HIGH)
  sys.exit()                



def zero_EL():
  az_direction = False
  az_steps = 0
  el_direction = False
  el_steps = 25
   
  while GPIO.input(13) == 0:
    buzz(1000,0.1)
    thread_move_steps(az_direction,az_steps,el_direction,el_steps)
  
  global current_el_pos
  current_el_pos = 0
   
def tracker(requested_sat):
  global current_az_pos
  global current_el_pos
  global lat
  global long
  global location_tz_offset
  global stop_tracking
  global tracking_sat_pos
  global tracking_sat_cat

  if lat == None or long == None:
     return "cant track. lat long not set"

  location = wgs84.latlon(lat, long)
  location_tz = timezone(timedelta(hours=location_tz_offset))

  ts = load.timescale()

  if os.path.exists("data/ssb/filtered_TLE.txt") and os.path.exists("data/fm/filtered_TLE.txt"):
    fm_satellites = open('data/fm/filtered_TLE.txt', 'r').read()
    ssb_satellites = open('data/ssb/filtered_TLE.txt', 'r').read()
    both = fm_satellites + ssb_satellites
    f = BytesIO(str.encode(both))
    satellites = list(parse_tle_file(f, ts))
  else:
     return "filtered_TLE not found. create it using 'Make/Update TLE via CelesTrak' on Config page"



  for satellite in satellites:
      if requested_sat in satellite.name:
          sat_to_track = satellite
  
  tracking_sat_cat = sat_to_track.model.satnum
  sat_status = "unknown"
  last_sat_status = "unknown"
  while True and not stop_tracking:
      #let first move settle before next move
      if sat_status == "unknown":
         loop_sleep = 1
      else:
         loop_sleep = 4

      difference = sat_to_track - location
      topocentric = difference.at(ts.utc(ts.now().utc_datetime() + timedelta(seconds=5))) #lead the sat a bit 
      alt, az, distance = topocentric.altaz()
      print(f'AZ:{az}, EL:{alt}')
      tracking_sat_pos = f'AZ: {az}, EL: {alt}<br>'.replace("deg","°")

      desired_az_pos = az.degrees
      az_steps, az_direction = az_deg_to_steps_dir(desired_az_pos)
      print(f'az_steps: {az_steps}')
      
      desired_el_pos = alt.degrees
      if desired_el_pos < 0 and current_el_pos > 0:
         desired_el_pos = 0
      el_steps,el_direction = el_deg_to_steps_dir(desired_el_pos)
      print(f'el_steps: {el_steps}')

      thread_move_steps(az_direction,az_steps,el_direction,el_steps)
      if az_steps > 0:
        current_az_pos = desired_az_pos
      if el_steps > 0:
        current_el_pos = desired_el_pos

      print("sat_status:" + sat_status)
      if float(current_el_pos) > 0:
         sat_status = "up"
      else:
         sat_status = "down"
      if sat_status == "up" and last_sat_status not in ["up"]:
        buzz(1000,0.1)
        buzz(500,0.1)
        buzz(1000,0.1)
      last_sat_status = sat_status
      sleep(loop_sleep)

def manual_move():
   global current_az_pos
   global current_el_pos
   while True:
    desired_az_pos = int(input('Move to Absolute AZ°: '))
    desired_el_pos = int(input('Move to Absolute EL°: '))
    az_steps, az_direction = az_deg_to_steps_dir(desired_az_pos)
    el_steps,el_direction = el_deg_to_steps_dir(desired_el_pos)
    thread_move_steps(az_direction,az_steps,el_direction,el_steps)
    if az_steps > 0:
      current_az_pos = desired_az_pos
    if el_steps > 0:
       current_el_pos = desired_el_pos
   

signal.signal(signal.SIGINT, handler)
if __name__ == '__main__':
    app.run(host='0.0.0.0',port=8443,ssl_context=("cert.pem", "key.pem"))

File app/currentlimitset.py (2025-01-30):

from RpiMotorLib import RpiMotorLib
import RPi.GPIO as GPIO
import concurrent.futures
import sys
import signal

GPIO.setwarnings(False)
GPIO.setmode(GPIO.BCM)
GPIO.setup(4, GPIO.OUT)#enable pin 
GPIO.output(4, GPIO.LOW)#enable pin

az_direction_pin = 20      
az_step_pin = 21
az_mode_pins = 22, 23, 24
az_a4988_nema = RpiMotorLib.A4988Nema(az_direction_pin, az_step_pin, az_mode_pins, "A4988")

el_direction_pin = 16    
el_step_pin = 17
el_mode_pins = 25, 26, 27
el_a4988_nema = RpiMotorLib.A4988Nema(el_direction_pin, el_step_pin, el_mode_pins, "A4988")

steptype = "Full"
stepdelay = 0.0005
verbose = False
initialdelay = 0.05

def handler(signum,frame):
  print("exiting... stopping motors and cleaning up GPIO")        
  az_a4988_nema.motor_stop()
  el_a4988_nema.motor_stop()
  GPIO.output(4, GPIO.HIGH)
  sys.exit()         

signal.signal(signal.SIGINT, handler)

with concurrent.futures.ThreadPoolExecutor() as executor:
        f1 = executor.submit(az_a4988_nema.motor_go, False, steptype , 0, stepdelay, False, initialdelay)
        f2 = executor.submit(el_a4988_nema.motor_go, False, steptype , 0, stepdelay, False, initialdelay)

input("Press any key to end...")

az_a4988_nema.motor_stop()
el_a4988_nema.motor_stop()
GPIO.output(4, GPIO.HIGH)
GPIO.cleanup()

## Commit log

2025-01-29 init commit
    [bom.csv, designators.csv, positions.csv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]
2025-01-29 improved UI buttons. fixed bug in moveTo func
2025-01-29 smoothed out Az movement. fixed a moveTo->tracker EL bug,
    [tracker.py]
2025-01-30 adding a4988 current limit mode script
2025-02-04 slowed AZ motor for smoother running. updated TLEs
2025-02-04 add 3d models
    [new_EBbox_base.stl, new_EBbox_top.stl, new_endstop_arm.stl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]
2025-02-07 updating pcb files
    [bom.csv, positions.csv]
2025-02-07 adding pcb image and schem
